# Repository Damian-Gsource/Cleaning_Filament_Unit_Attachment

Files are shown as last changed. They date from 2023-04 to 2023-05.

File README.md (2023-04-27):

# Cleaning_Filament_Unit_Attachment
This 3D Printer attachment helps prevent clogging by adding a cleaning unit onto which a cloth can be inserted into. This unit will add another step which the 3D filament will have to pass through, and it will help pick up any large particles such as dust or shavings. It should be attached vertically onto the platform on which the 3D Printer is

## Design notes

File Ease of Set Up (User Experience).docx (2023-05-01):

Purpose:

Since this device is meant to be used by a variety of individuals due to its goal of being an open source device, we would like for it to be easy to set-up. In order to gauge ease of use we will use a user defined scale. With the assumption that whoever will be using the device is familiar to 3D printing, the test subjects would fall under this category and would be instructed to perform self evaluations using the following table:

Rank | Description
1 | The device cannot be set up, even with assistance
2 | The device can be set up with assistance from a trained professional
3 | The device can be set up while consulting an Assembly Manual
4 | The device can be set up independently after several attempts
5 | The device can be set up independently on first attempt

Target Test Criteria: Average Score ≥4

Results:

Responses: 40

Average Score: 3.91875

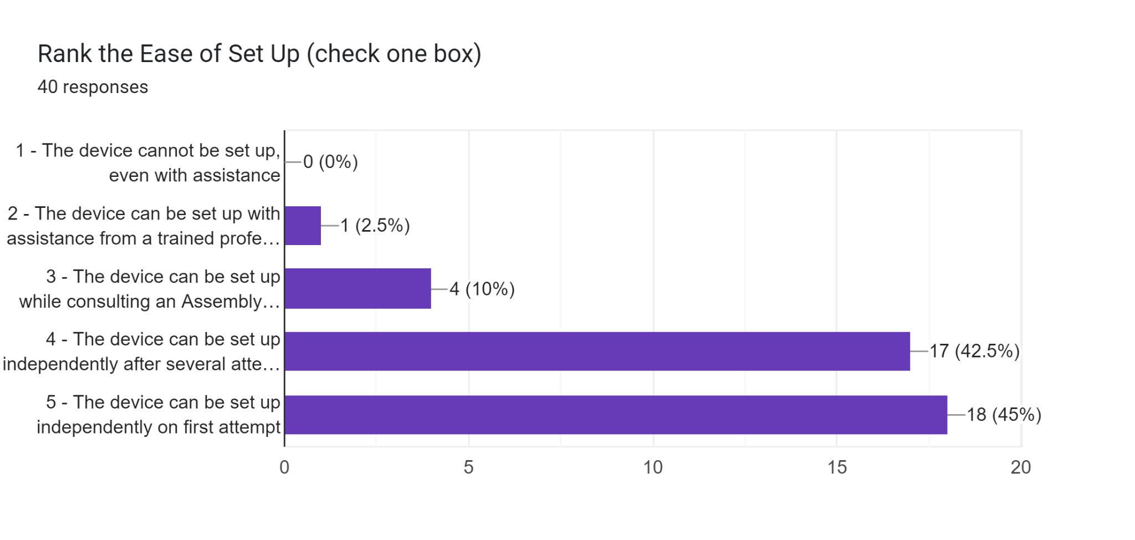
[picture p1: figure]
Forms response chart. Question title: Rank the Ease of Set Up (check one box) . Number of responses: 40 responses.

It should be noted that we changed our manual based on observations and recommendations that we and the participants noticed throughout the entirety of the experiments. If the participant didn’t need the manual, they didn’t have any input to the manual. It should be noted that the majority of the population that we tested had at least some experience with a 3D printer, with a few outliers who didn’t have any experience with it.

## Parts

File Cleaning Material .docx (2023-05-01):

Purpose:

Since the main component that cleans the filament is the material in the housing unit of the device, we need to make sure the material doing the cleaning is the best at its job. The previous team performed this test with 5 materials, but did so with their arbitrary measurement of what it means to be clean. Therefore, in order to determine this function accurately, we will perform this test as an add-on to the overall Cleaning Assessment; using a printing assessment to see whether or not the print will fail as a result of clogging.

Material Type | Day 1 Update | Day 2 Update | Day 3 Update | Day 4 Update | Day 5 Update
MicroFiber Cloth | Printing | Filament broke (Fixed and Resumed) | Printing | Printing | Printing
Swiffer Cloth | Clogged (GEAR) | Printing | Clogged (GEAR) | Clogged (GEAR) | N/A
MicroFiber Towel | Printing | Printing | Clogged (GEAR) | Printing | (Clogged) GEAR

It must be noted that all sources of failure occurred either as a result of the wheel getting clogged from strands of the cloth or due to the fact that there was too much friction that caused the filament breaking inside the housing unit and/or tube.

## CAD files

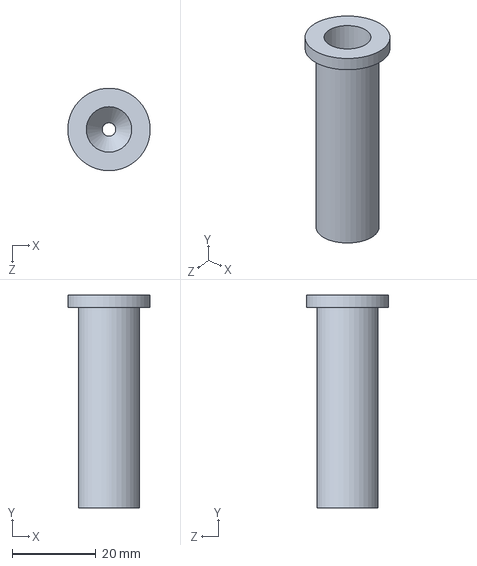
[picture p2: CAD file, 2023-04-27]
dustbust_housing_v2_print.SLDPRT
19.7 x 50.8 x 19.7 mm

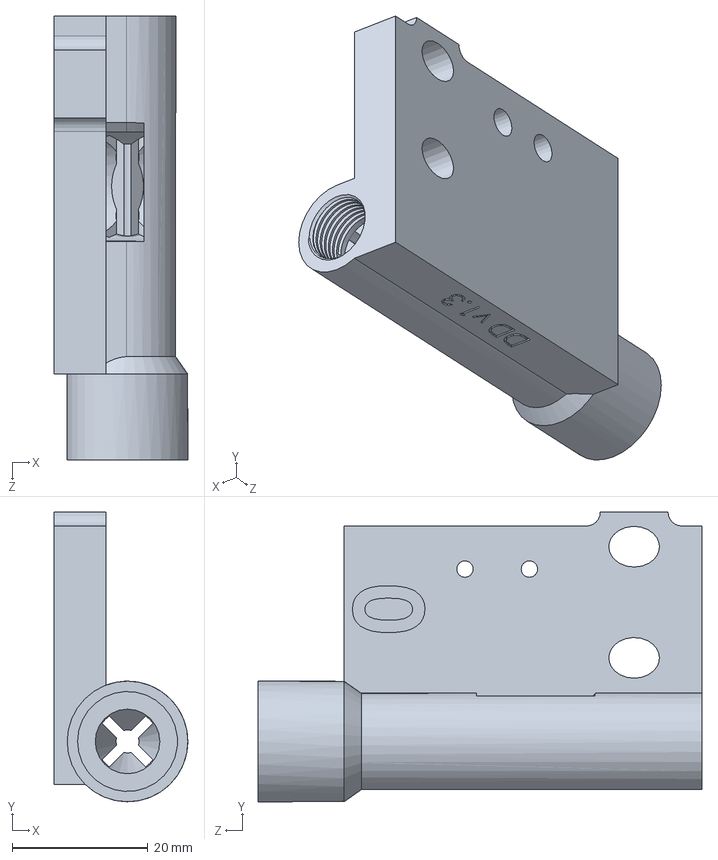
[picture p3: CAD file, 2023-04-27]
dustbust_fdu_v1 (3).SLDPRT
19.7 x 42.7 x 65.4 mm

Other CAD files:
dustbust_fdu_v1.STL
dustbust_housing_v2_print.STL

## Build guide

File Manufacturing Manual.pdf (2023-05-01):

Manufacturing Manual
Goal: Open Source
To include:
- Bill of Materials
- Estimated Costs
- Step by Step instructions (visuals + text)
- Attach CAD file
- DFM plan (design considerations for other manufacturing methods–i.e. injection molding)

Product Overview
The Dust Remover is an open source 3D printed solution to removing dust from 3D printing filament just before it is extruded. The body of it is to be entirely 3D printed and friction fit, eliminating complex in-house manufacturing processes like gluing or stopping the print halfway to fit magnets in. It also requires two extra non-printed parts that are easy to find or buy: a microfiber cloth and a zip tie. The product currently interfaces with Re:3D’s FDU (filament detection unit), but it can be used apart from it as well.

Bill of Materials
The following bill of materials is for one device, not including the FDU components.
Material | Cost per unit | Amount used per unit
3D printer filament, PLA or PETG | $0.45 | 22.4g of filament
Microfiber Cloth | About $0.20 | 4x3” piece of cloth
Zip tie, plastic (one time use) or velcro (reusable) | <$0.05 or $0.18 | 1 zip tie

Assembly Instructions
1. Print the cloth housing unit (HU) on a 3D printer with at least a 10% infill and 1.5 mm wall thickness. Place the unit on the printer bed with the flat face of the cylinder on the bed and the lipped end on top. Add supports around the lip and print with a brim to reduce the chance of the print warping off the bed. See Figure 1 for how this should look on a Prusa Slicer software.
2. Print the filament detection unit (FDU) on a 3D printer with at least 10% infill and 1.5 mm wall thickness. Place the unit on the printer bed as shown in Figure 2. Print with no supports.
3. Cut the microfiber cloth into a 4x3” rectangle with scissors. The rectangle does not need to be very precise.
4. The cut microfiber cloth may have bits of fluff that fall off the edges after it’s cut. Pull at the edges of the cut microfiber cloth by hand until no more small bits of the cloth come off.
5. Take the end of the filament that you are about to put in the extruder and wrap the cloth around it, with the 4” longer end lined up with the filament.

6. Push the wrapped filament into the lipped end of the housing unit as far as you can. Push the filament through until it sticks out the small hole on the opposite end of the housing unit.
7. Peel the cloth that is sticking out above the lip down and around the sides of the lip.
8. Take the zip tie (plastic or velcro) and wrap it around the cloth that you peeled down, just below the housing unit’s lip.
9. Tighten the zip tie to secure the cloth to the housing unit.
10. If using an FDU, fit the smaller non-lipped end of the housing unit into the mouth of the FDU. It is friction fit, so a small amount of force will be needed to push it in.
11. Push/pull the filament through until it sticks out of the FDU. Now, you can feed the filament through the extruder. The device should now be actively cleaning the filament as the printer extrudes.

CAD Images

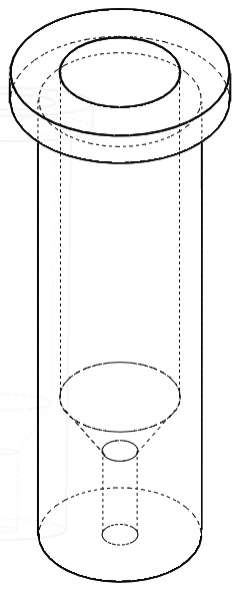
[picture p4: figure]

Figure 1: 3D printed housing unit structure with internal structure illustrated

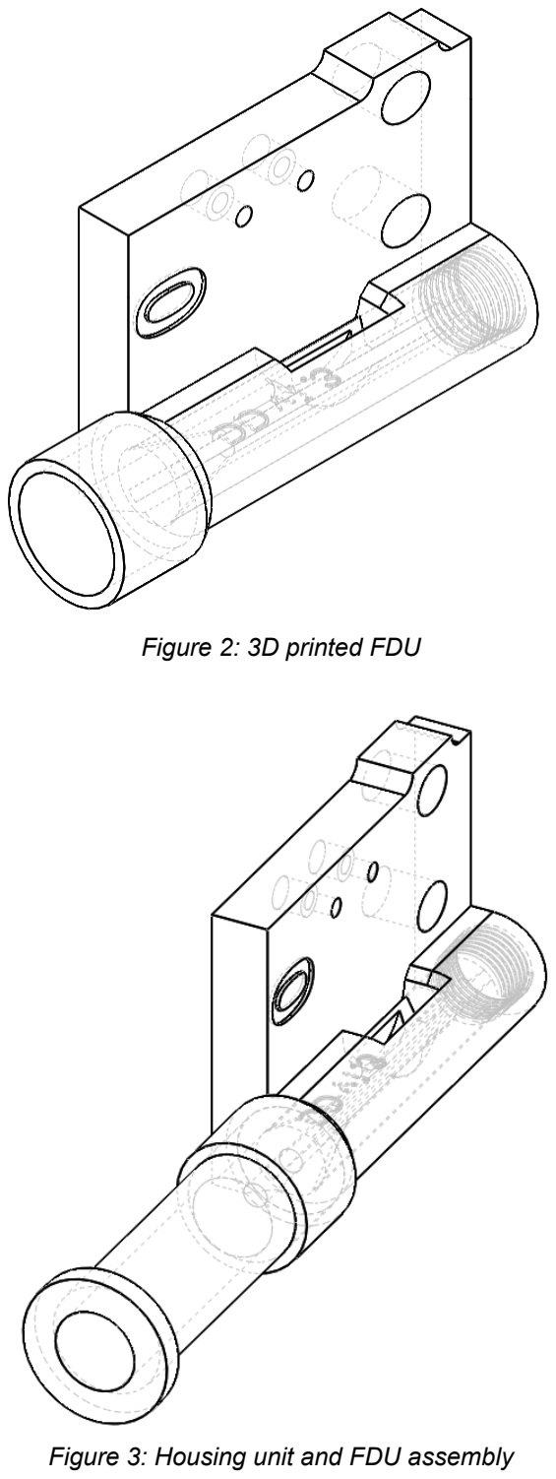
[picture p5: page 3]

Figure 2: 3D printed FDU

Figure 3: Housing unit and FDU assembly

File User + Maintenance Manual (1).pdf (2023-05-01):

User + Maintenance Manual

Guides to include:
- Quick Start Guide
- User Guide
- Maintenance Guide
- Troubleshooting Guide

## User Guide and Maintenance Manual for Filament Dust Remover

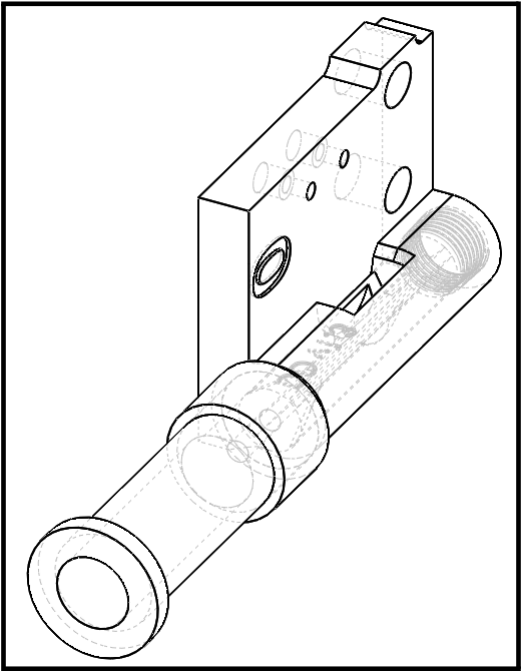
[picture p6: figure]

Figure 1: CAD image of the Filament Dust Remover

Authors: Daniel Plascencia, Damian Gonzalez, Ellice Gao, Rubén Marroquin

### Contents

### Introduction

Overview:
This document provides multiple guides that are designed to be easily and readily available to help users of the Filament Dust Remover with any problems they may face. These problems could arise from installing, understanding how it works, how to maintain it, and other general issues that can occur throughout the product’s lifetime.

To ensure full comprehension of how the device works and get the most out of it, please read the following manuals carefully and use the product as directed.

### Parts and Their Functions (Front Views)

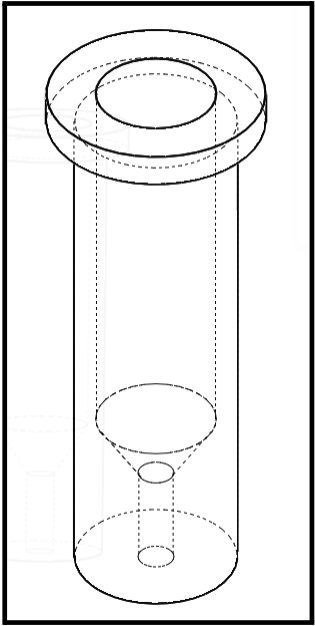
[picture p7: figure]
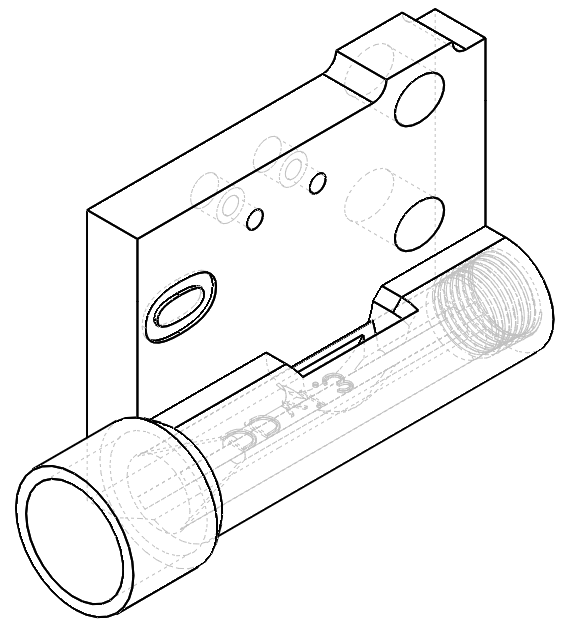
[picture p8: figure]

Part 1 | Part 2
1. Housing Unit (HU)
This houses the cleaning material that will remove dust from filament as it passes through
2. Filament Detection Unit (FDU)
This houses the mechanism that detects if filament is running through the device or not

### Quick Start Guide

1. Print the Filament Detection Unit (FDU) and the Housing Unit (HU).
2. Get microfiber cloth and cut out a 4x3” rectangle.
3. Cut an X-shaped slit in the center of the rectangle.
4. Insert the microfiber cloth into the HU and secure it using the zip tie.
5. Feed the filament through the HU and FDU (while they are still separate).
6. Insert the HU into the FDU using the pressure fit.
7. Attach the assembled piece vertically onto a surface.
8. Use your 3D printer and enjoy your clean prints!

### User Guide

Cleaning Material Set Up
1. Cut material into a rectangle (~ 4x3 in)
2. Tug at sides of material to get rid of fluff
3. Take filament and wrap it with the cleaning material. Make sure that the fluffy side touches filament. Wrap tightly on one end of the filament, more specifically the side that will be going into housing
4. Insert filament wrapped material into housing, use twisting motion
5. Unwrap exposed side of filament and wrap that over the housing
6. Take a velcro zip tie and wrap it around the material/housing. Make sure that the soft side of the velcro zip tie touches material. Once that is achieved, then make sure to tie tightly
7. Put the housing into the FDU

Assembling HU and FDU
To assemble the device, press fit the HU into the FDU. This enables a sturdy connection, yet is easily removable with a little force. If it seems to be too tight, then you can twist the two units in opposite directions to take them apart.

Getting it ready to use
Run the filament through the assembled device and find a surface on which to attach the device. This could be on the side of the 3D printer or any surface that allows for the device to be secured and for the filament to linearly pass through.

WARNING: The warnings for the care and handling of the Filament Dust Remover are listed below

- Do not secure the assembled device in an orientation that bends that filament.
- When running for long periods of time, the device may get really dirty. This is part of the design and means the device is working as intended
- Incorrect handling, such as jamming the cleaning material into the HU may cause a blockage and not allow the filament to run through and get cleaned.

- Do not set the device with filament entering through the FDU and exiting out the HU, it is not made to work in this manner.
- Do not leave the device unsecured, this may lead to the device hitting parts of the printer.

### Maintenance Guide

Once the HU gets too dirty, remove and replace the cleaning material with a new one.

### Troubleshooting Guide

Challenge | Potential Solution
HU doesn’t fit into FDU | ● Reduce the thickness of the printing layers to insure a press fit
Cleaning material causes friction, preventing filament from running through | ● Apply less cleaning material ● Check that the material is touching the filament, but not squeezing tightly
Filament diameter is too big for device | ● Download the attached CAD file and edit the diameter of the device ● Use smaller diameter filament

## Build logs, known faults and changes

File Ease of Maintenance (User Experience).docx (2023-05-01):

Purpose:

Since this device is meant to be used by a variety of individuals due to its goal of being an open source device, we would like for it to be easy to maintain as well as be simple to upkeep. In order to gauge ease of maintenance we will use a user defined scale. We will have the user take apart the dust remover, replace the part with another 3d printed item, and put it back together again. This set of tasks will be our definition of “maintain”. With the assumption that whoever will be using the device is familiar to 3d printing, the test subjects would fall under this category and would be instructed to perform self evaluations using the following table:

Rank | Description
1 | The device cannot be maintained, even with assistance
2 | The device can be maintained with assistance from a trained professional
3 | The device can be maintained while consulting an Assembly Manual
4 | The device can be maintained independently after several attempts
5 | The device can be maintained independently on first attempt

Target Test Criteria: Average Score ≥4

Results:

Responses: 39

Average Score: 3.57

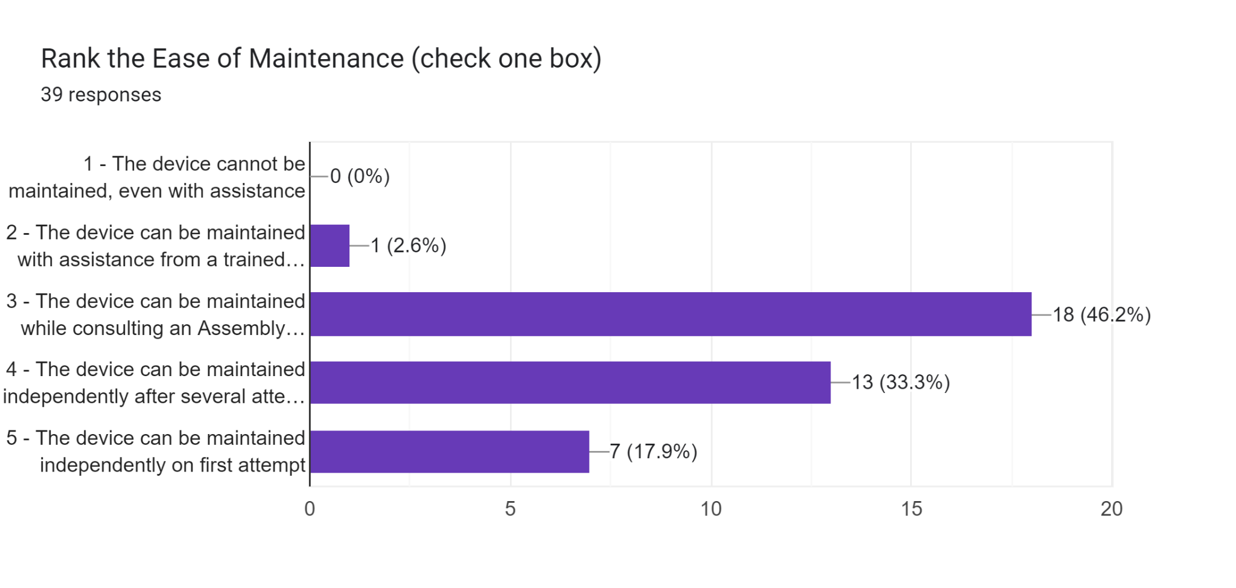
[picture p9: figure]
Forms response chart. Question title: Rank the Ease of Maintenance (check one box) . Number of responses: 39 responses.

It should be noted that we changed our manual based on observations and recommendations that we and the participants noticed throughout the entirety of the experiments. If the participant didn’t need the manual, they didn’t have any input to the manual. It should be noted that the majority of the population that we tested had at least some experience with a 3D printer, with a few outliers who didn’t have any experience with it.

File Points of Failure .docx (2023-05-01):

Introduction:

A point of failure assessment is a systematic evaluation of a system or component to identify potential points of failure. This assessment is essential for identifying and mitigating risks, improving reliability, and ensuring overall functionality of the system.

Identifying Potential Points of Failure:

The first step in a points of failure assessment is to identify potential points of failure. We have found in our parts that the points of failure that could arise from our part are due to the friction between the cleaning material and the filament causing the part to continually increase until the filament actually becomes stuck. This causes the filament to rip inside the tube. And thus cause a failure. The next point of failure that could arise from this part is when the filament tears away strands from the cleaning material, causing the filament to act as a carrier for the strands which then starts to mess up the wheels.

Assessing Risk:

Once potential points of failure have been identified, the next step is to assess the risk associated with each failure mode. The risks that are associated with these materials are that they can either cause the filament to break inside the tube or they can cause the gear to get stuck. So far, no point of failure has been identified as a result of clogging.

Mitigating Risks:

After identifying potential points of failure and assessing the associated risks, the next step is to develop strategies for mitigating these risks. In order to get the result that we want, we will have to choose the appropriate cloth and conduct the appropriate method of applying the cloth to the part.

Conclusion:

A point of failure assessment is a critical process for identifying potential risks and mitigating those risks to improve system reliability and functionality. This points of failure assessment has shown us that by using the
